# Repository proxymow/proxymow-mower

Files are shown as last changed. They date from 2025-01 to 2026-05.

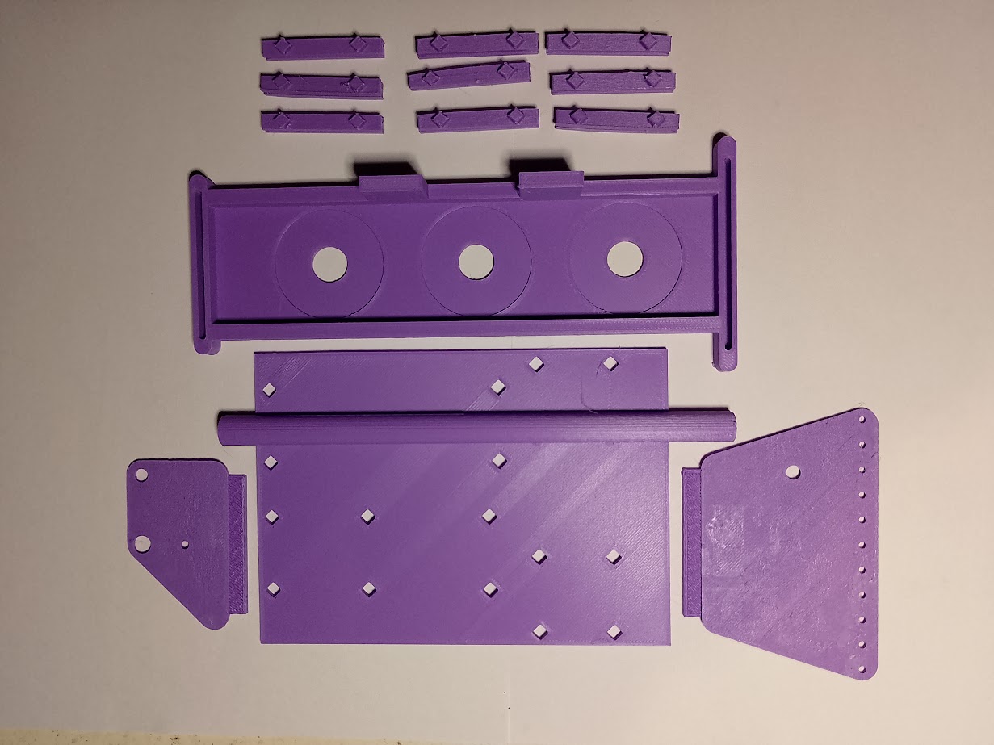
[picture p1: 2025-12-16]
3dprint-tracks/electronics-chassis/printed parts.jpg

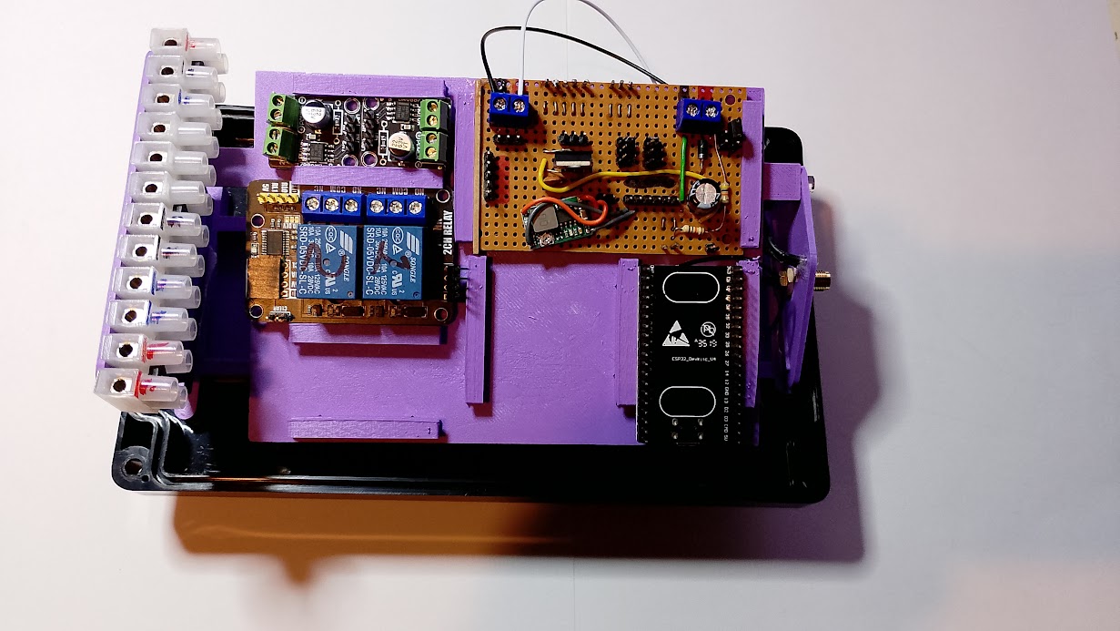
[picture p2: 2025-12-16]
3dprint-tracks/electronics-chassis/assembly.jpg

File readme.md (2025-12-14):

# Proxymow Automated Robot Lawn Mower (Mower)
## What the project does
Proxymow is a robotic lawn mower system that uses computer vision to locate and guide the mower. This repository contains the MicroPython source code for the mower device. The sister repository [Proxymow Server](https://github.com/proxymow/proxymow-server) contains the source code for the server.

## Why the project is useful
Proxymow differs from many robotic mowers:
* Does not rely on vulnerable boundary wires
* Does not use GPS or Bollards
* Does not need to be taught a route, supports plug-in mowing patterns
* Employs very low cost technology: Rasperry Pi, NodeMCU, RPI Pico, ESP32

## Getting started
Clone or Download the repo and change directory to the installation folder.

Edit utils.py to set up Wi-Fi access, and schematic.py to *wire up* your mower.

Use Thonny, or rshell to deploy the following MicroPython files to your device:
* main.py
* mower.py
* schematic.py
* utils.py
* shared_utils.py
* artic.py
* umotion_lib.py

Reset the device and use the test client to issue some commands:
```
    cd clients; python udp_client.py 
```

## Getting help
Read the documentation [module information](https://proxymow.co.uk/mower).

## Who maintains and contributes to the project
info@proxymow.co.uk

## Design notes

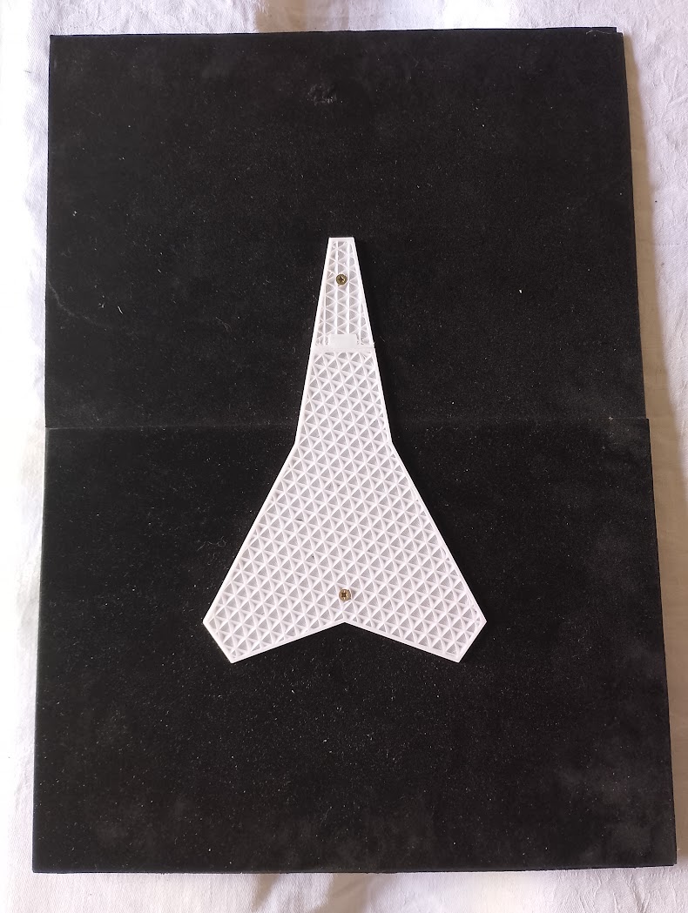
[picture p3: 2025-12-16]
3dprint-tracks/target/target mounted.jpg

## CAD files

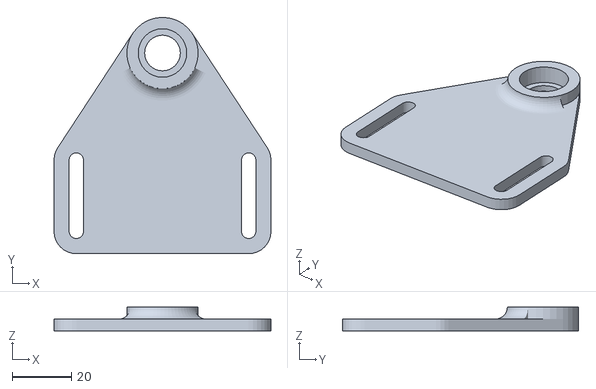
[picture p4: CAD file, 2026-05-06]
3dprint-tracks/bearing-plate/Bearing BackPlateMk2.stl
73.0 x 79.5 x 8.00

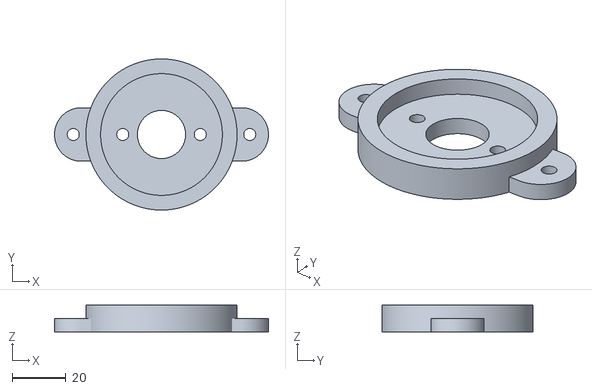
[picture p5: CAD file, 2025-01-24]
3dprint-tracks/cutter-motor-bracket/Cutter-Motor-Bracket.stl
80.0 x 56.5 x 10.0

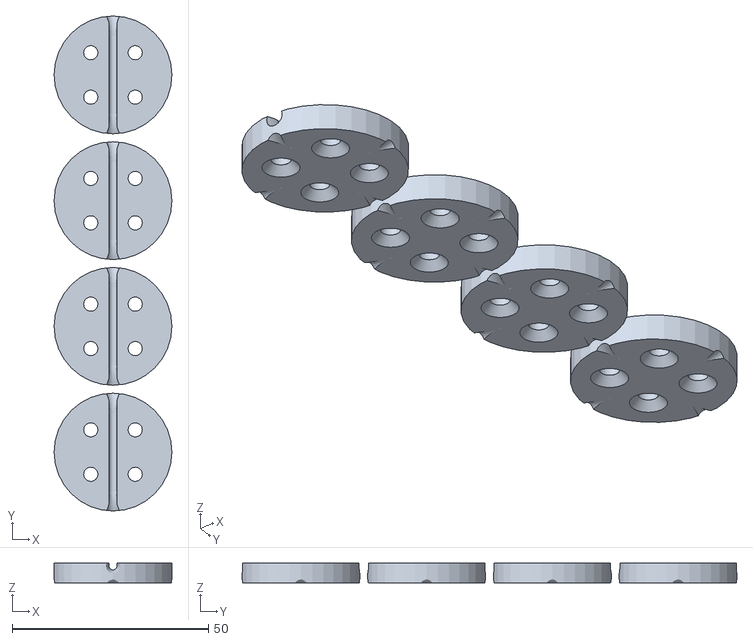
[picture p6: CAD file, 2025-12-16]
3dprint-tracks/cutter-wire-stack/Cutter-Wire-Stack.stl
30.0 x 126.0 x 5.00

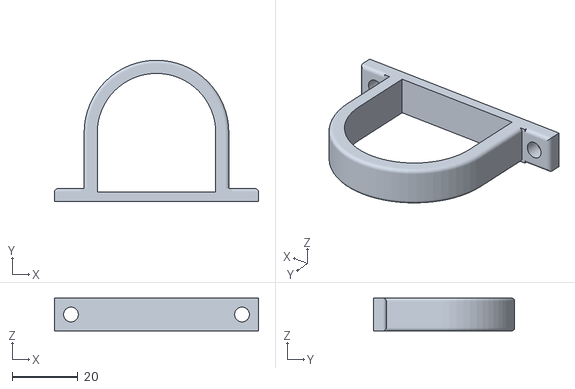
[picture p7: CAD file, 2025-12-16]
3dprint-tracks/drive-motor-bracket/Planetary Motor Bracket.stl
62.0 x 43.0 x 10.0

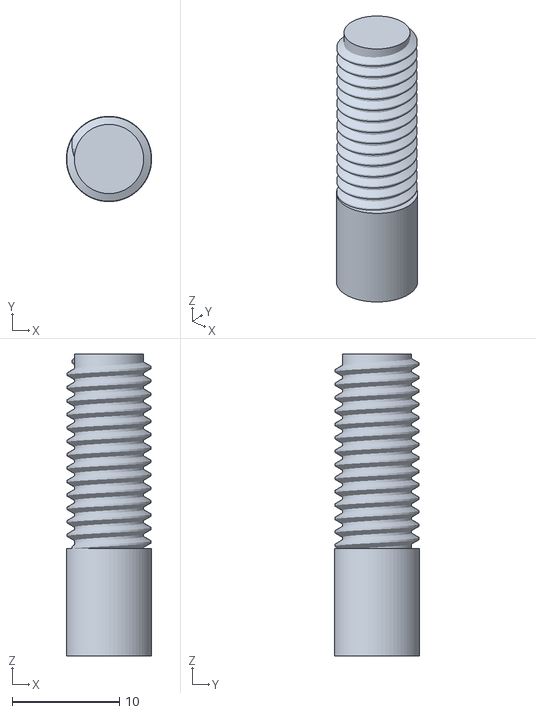
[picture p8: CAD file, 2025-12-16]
3dprint-tracks/drive-sprocket/Drive Sprocket Shaft.stl
7.95 x 7.95 x 28.1

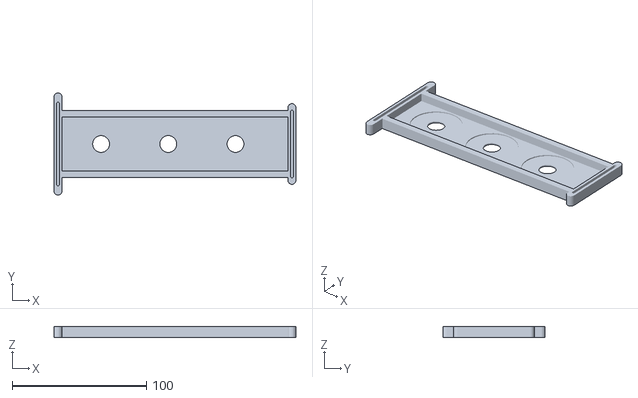
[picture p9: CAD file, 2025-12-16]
3dprint-tracks/electronics-chassis/chassis-base.stl
180.0 x 76.0 x 8.00

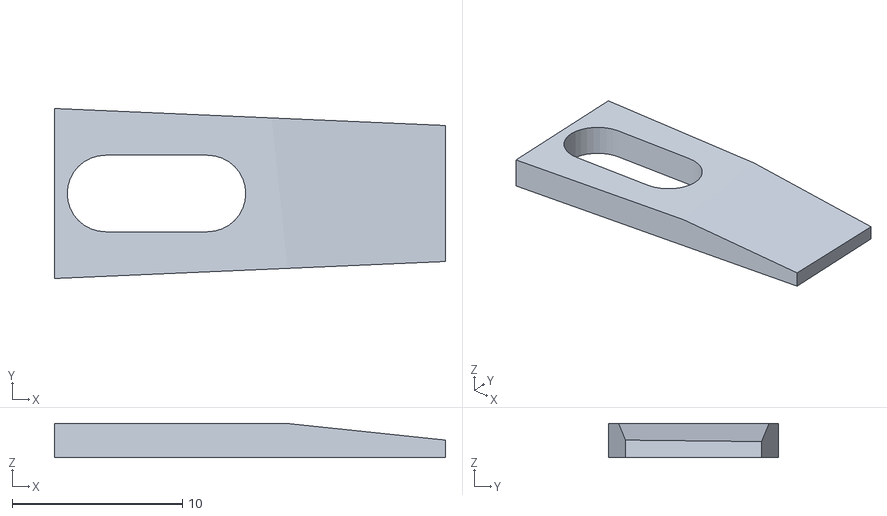
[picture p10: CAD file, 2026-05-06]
3dprint-tracks/idler-hub/scraper.stl
23.0 x 10.0 x 2.00

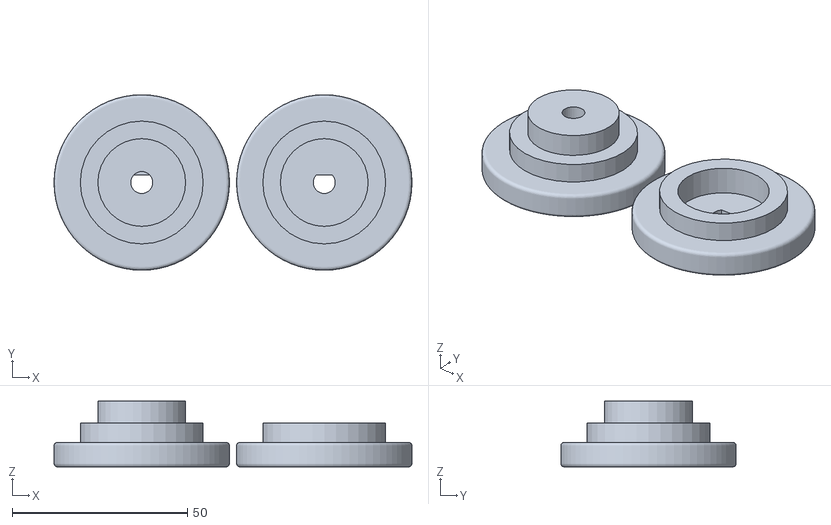
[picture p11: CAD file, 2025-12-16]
3dprint-tracks/idler-wheel/Idle Wheel.stl
102.0 x 50.0 x 18.8

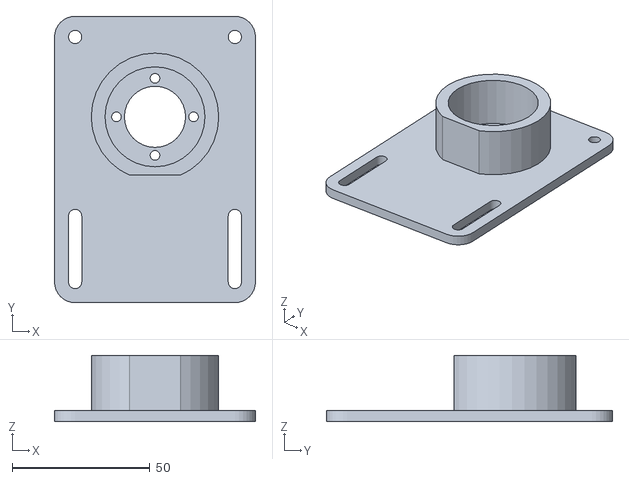
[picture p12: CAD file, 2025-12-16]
3dprint-tracks/motor-plate/Motor Plate.stl
73.0 x 104.0 x 24.0

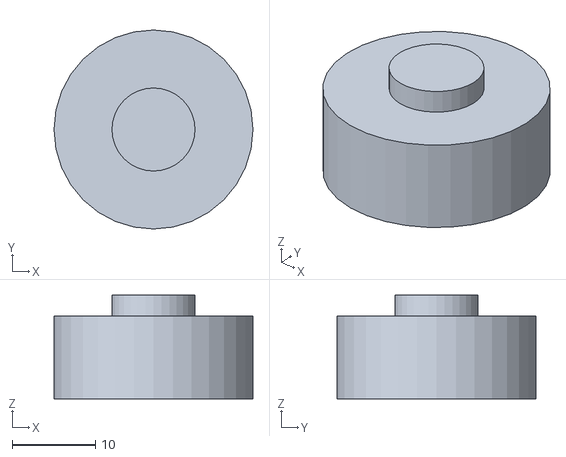
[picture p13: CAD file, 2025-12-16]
3dprint-tracks/roof-socket/Roof Plug.stl
23.9 x 23.9 x 12.5

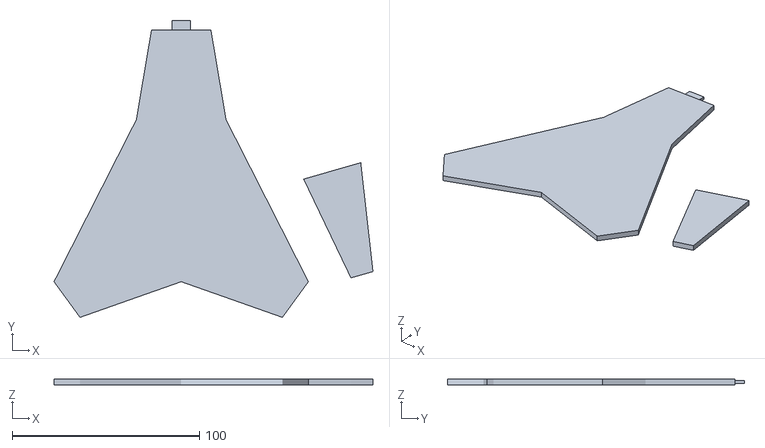
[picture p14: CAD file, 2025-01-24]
3dprint-tracks/target/Target-230.stl
170.2 x 158.3 x 3.00

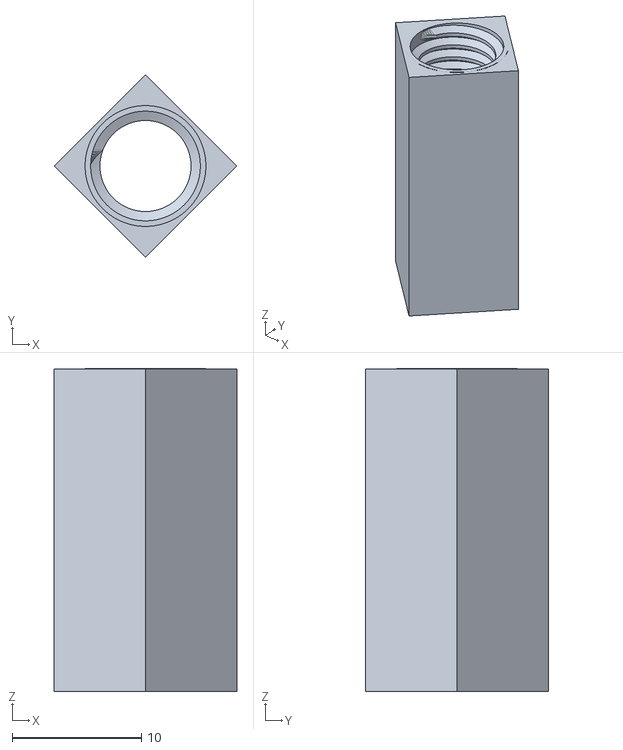
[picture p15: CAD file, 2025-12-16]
3dprint-tracks/tension-rod-adaptor/Hub Threaded Insert.stl
14.1 x 14.1 x 25.0

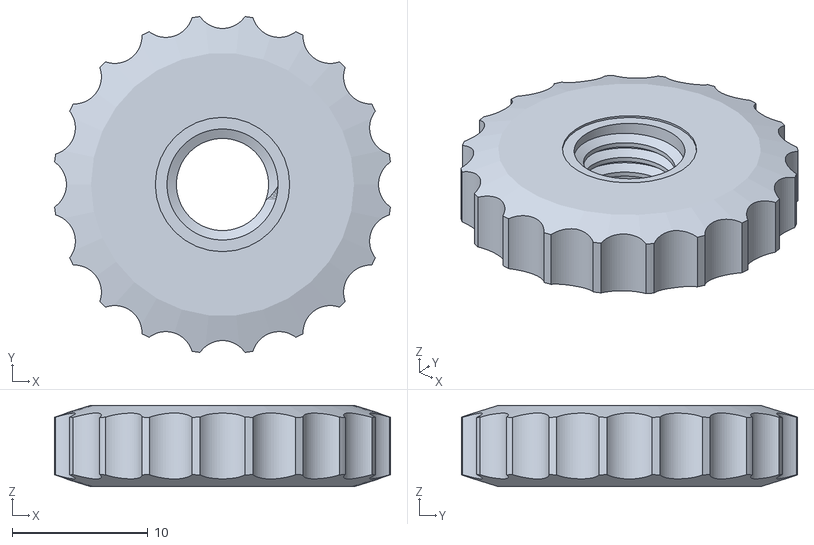
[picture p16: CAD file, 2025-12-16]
3dprint-tracks/thumbwheels/Thumbwheel.stl
24.8 x 24.8 x 6.00

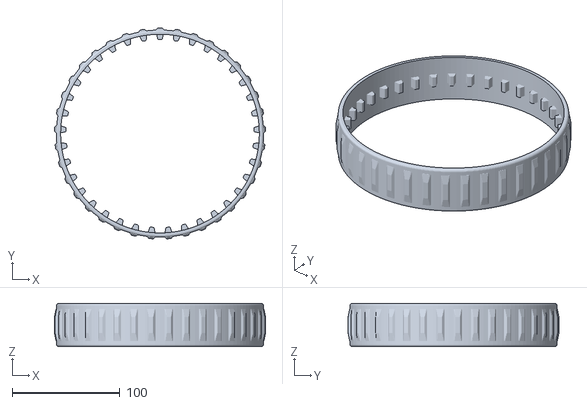
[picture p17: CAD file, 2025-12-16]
3dprint-tracks/track/Belt.stl
196.0 x 195.9 x 40.0

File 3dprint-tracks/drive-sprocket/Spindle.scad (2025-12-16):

//Spindle for Sprocket Components
include <../shared/Constants.scad>
use <threadlib/threadlib.scad>

module dee_shaft(hgt, dia, offset) {
    difference() {
        cylinder(h=hgt, d=dia, center=true, $fn=32);
        translate([0, dia - offset, 0]) cube([dia, dia, hgt+0.1], center=true);
        translate([0, -(dia - offset), 0]) cube([dia, dia, hgt+0.1], center=true);
    }
}

module spindle() {
     {
        rotate([0, 180, 0]) difference() {
            union() {
                cylinder(h=spindle_length, d=spindle_outer_dia, $fn=6, center=true);
                translate([0, 0, (spindle_length + spindle_shoulder_width)/2]) cylinder(h=spindle_shoulder_width, d=spindle_shoulder_dia, $fn=32, center=true);
            }
        translate([0, 0, (spindle_drive_shaft_length + 0.1)/2]) dee_shaft(spindle_drive_shaft_length, spindle_dee_shaft_dia, spindle_dee_shaft_offset);
        translate([0, 0, -(spindle_length/2)]) cylinder(h=spindle_length + 2, d=spindle_bearing_shaft_dia, center=true, $fn=32);
        }
        translate([0, 0, 0.5]) scale([spindle_thread_x_factor, spindle_thread_y_factor, spindle_thread_z_factor]) nut("M8", turns=spindle_thread_num_turns, Douter=9, $fn=6);
    }
}

spindle();

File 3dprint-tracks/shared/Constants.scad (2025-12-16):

/*
    Constants.scad contains all the global constants
*/
use <Tooth Profile.scad>

//idler hub
idle_bearing_od = 16;//mm
idle_bearing_fit_dia = idle_bearing_od * 1.03;//push-in fit for bearing
idle_bearing_thickness = 5.25;//push-in fit
hub_thickness = 15;
hub_dia = 24;
idle_shaft_hole_dia = 6.5;//clearance for 6mm shaft
scraper_fix_hole_dia = 4.5;//mm
idler_width = 25;//mm
idler_dia = 50;//mm
idler_spacing = 0.5;//mm
radial_spacing = 5;//mm
tube_insertion = 25;//mm
tube_outer_dim = 10;//10mm square tube
tube_dim = sqrt(tube_outer_dim^2 + tube_outer_dim^2) * 1.04;
echo("tube_outer_dim:", tube_outer_dim, "tube_dim:", tube_dim);

//idler wheel
idle_wheel_thickness = 25;
idle_wheel_dia = 50;
idle_shaft_dia = 6.25;//mm
tooth_space_thickness = 11;//mm
tooth_space_dia = 35;//mm
runner_thickness = (idle_wheel_thickness - tooth_space_thickness)/2;
edge_radius = 1;
dee_shaft_offset = 1;
spigot_scale_factor = 1.0;//grow spigot hole if necessary for a tight fit

//idler axle
idle_rod_dia = 5.92;//mm tight fit for bearing
idle_rod_length = 25 + (2 * 0.5) + (2 * 15) + (2 * 2);//mm idler width + 2 spacers + 2 hubs + 2 washers
echo("idle_rod_length", idle_rod_length);
idle_rod_cap_length = 2;//mm
idle_rod_clip_width = 1;//mm
idle_rod_clip_dia = 4.5;//mm

//knurled wheel and locknut
//knob parameters
KNOB_DIAM=25;
//screw parameters
SCREWHEAD_FACETOFACE=0;
SCREWHEAD_DEPTH=12;
THRU_HOLE_DIAM=9.5;
//grippy cutouts parameters
NUM_GRIP_CUTOUTS=20;
GRIP_CUTOUT_DIAM=4;
CUTOUT_RADIUS_ADJ=1;
KNURLED_WHEEL_HEIGHT=6;
KNURLED_WHEEL_NUM_TURNS = 3.5;
LOCKNUT_HEIGHT=3;
LOCKNUT_NUM_TURNS = 1.375;

//motor plate
gearbox_collar_hole_dia = 22.2;//mm
motor_plate_thickness = 4;//mm
motor_plate_corner_dia = 15;//mm
plan_motor_dia = 36.3;//mm
plan_shoulder_base_thickness = 3;// mm
plan_shoulder_thickness = 5;// mm
plan_shoulder_height = 20;// mm

//planetary motor bracket
pmb_motor_dia = 36;//mm 35.5 plus clearance
pmb_base_thickness = 3;//mm
pmb_foot_thickness = 5;//mm
pmb_width = 10;//mm
pmb_thickness = 4;//mm
pmb_chamfer_radius = 1;//mm
pmb_fix_hole_dia = 4.5;//mm

//bearing backplate
drive_bearing_bush_dia = 24;//mm
drive_bearing_od = 16;//mm
drive_bearing_fit_dia = drive_bearing_od * 1.02;//push fit for bearing
drive_bearing_recess = 6;//mm 

//drive sprocket
sprocket_spacing = 0.5;//mm
tooth_height = 5;//mm 4 + 1 to sink into cylinder

//tube clamp
clamp_width = 10;//mm
clamp_effect = 0.75;//mm
clamp_int_dia = 0.5;//mm
clamp_ext_dia = 2.5;//mm
clamp_fix_hole_dia = 4.8;//mm
clamp_washer_dia = 13;// for 12.5mm washer
clamp_washer_thickness = 1;//mm

//drive spindle
plan_motor_drive_shaft_dia = 8;//mm
spindle_outer_dia = 20;//mm fn=6 for hex
spindle_length = 25;//mm
spindle_shoulder_dia = 30;//mm
spindle_shoulder_width = 10;//mm
drive_sprocket_shaft_hole_dia = 8.32;//for 8mm shaft
spindle_dee_shaft_offset = 1;//mm
spindle_dee_shaft_dia = plan_motor_drive_shaft_dia * 1.0175;//mm interference fit
spindle_drive_shaft_length = 25;//mm shaft is 17.5 only 14mm of which is D'eed
spindle_bearing_shaft_dia = 9.3;//space for M8 thread
spindle_thread_num_turns = 9;
spindle_thread_x_factor = 1.04;
spindle_thread_y_factor = 1.04;
spindle_thread_z_factor = 1.0;

//drive sprocket shaft
drive_sprocket_shaft_num_turns = 14;
bearing_section_length = 10;//mm
back_bearing_stub_dia = 7.95;//mm for 8mm hole in bearing

//drive sprocket cog
tth_num_teeth = 9;
tth_pitch_angle = 360 / tth_num_teeth;
drive_sprocket_dia = 50;
tooth_depression = 1.1;//to smooth base fillets
sprock_tooth_x_scale = 0.8;//put space between teeth
sprock_tooth_y_scale = 1.05;//
sprock_thickness = 11;//mm for a 7|11|7 sandwich
tth_sprock_press_angle = 5;
tth_tooth_pitch = 8;
tth_root_fillet_radius = 1;
tth_tooth_height = 5;
sprock_tooth_profile_pts = tooth_points(tth_sprock_press_angle, tth_tooth_pitch, tth_root_fillet_radius, tth_tooth_height);

//drive plain cog
plain_cog_dia = 50;
plain_cog_thickness = 7;
plain_cog_rim_thickness = 3;//mm

//just for assembly
wheelbase = 200;//mm horizontal distance between idle wheel centres
track_triangle_height = 60;//mm vertical distance between drive motor and tube centres

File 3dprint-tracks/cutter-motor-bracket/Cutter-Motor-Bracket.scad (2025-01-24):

/*
    Proxymow Mower - Cutter Motor Bracket
    For 775 Type 12V DC Motor
    Print in TPU to provide anti-vibration properties
*/
$fa=1;
$fs=0.4;
body_height = 10;//mm
body_dia = 56.5;//mm
cutout_height = 5;//mm
motor_body_dia = 45.5;//mm
motor_collar_dia = 18;//mm
motor_fixing_centres = 29;//mm
motor_fix_hole_dia = 4.5;//mm
fix_hole_dia = 4.5;//mm
foot_dia = 20;//mm
foot_height= 5;//mm
foot_extent = 30;//mm
fixing_centres = 66;//mm

module bracket_body() {
    //outer ring
    difference() {
        cylinder(h=body_height, d=body_dia);
        translate([0, 0, body_height/2]) cylinder(h=body_height, d=motor_body_dia);
    }
    //feet
    hull() {
        translate([foot_extent,0,0]) cylinder(h=foot_height, d=foot_dia);
        translate([-foot_extent,0,0]) cylinder(h=foot_height, d=foot_dia);
    }
}
module cm_bracket() {
    difference() {
        bracket_body();
        //central hole
        translate([0,0,-1]) cylinder(h=body_height, d=motor_collar_dia);
        //motor fixings
        translate([motor_fixing_centres/2,0,-1]) cylinder(h=body_height, d=motor_fix_hole_dia);
        translate([-motor_fixing_centres/2,0,-1]) cylinder(h=body_height, d=motor_fix_hole_dia);
        //mounting holes
        translate([fixing_centres/2,0,-1]) cylinder(h=body_height, d=fix_hole_dia);
        translate([-fixing_centres/2,0,-1]) cylinder(h=body_height, d=fix_hole_dia);
    }
}
cm_bracket();

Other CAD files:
3dprint-tracks/tube-clamp/Tube Clamp.stl
3dprint/battery-mount/Battery-Foot.stl
3dprint/component-tray/rp2-pico.stl
3dprint/drive-motor-bracket/Drive-Motor-Bracket.stl
3dprint-tracks/drive-motor-bracket/Planetary Motor Bracket.scad
3dprint-tracks/assembly/Assembly.scad
3dprint-tracks/bearing-plate/Bearing BackPlate.scad
3dprint-tracks/bearing-plate/Bearing BackPlate.stl
3dprint-tracks/bearing-plate/Bearing BackPlateMk2.scad
3dprint-tracks/cutter-wire-stack/Cutter-Wire-Stack.scad
3dprint-tracks/drive-sprocket/Drive Plain Cog.scad
3dprint-tracks/drive-sprocket/Drive Plain Cog.stl
3dprint-tracks/drive-sprocket/Drive Sprocket Cog.scad
3dprint-tracks/drive-sprocket/Drive Sprocket Cog.stl
3dprint-tracks/drive-sprocket/Drive Sprocket Shaft.scad
3dprint-tracks/drive-sprocket/Spindle.stl
3dprint-tracks/electronics-chassis/Chassis.scad
3dprint-tracks/electronics-chassis/chassis-platform.stl
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

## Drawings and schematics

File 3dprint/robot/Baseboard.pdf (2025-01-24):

## Cutout to aid alignment of

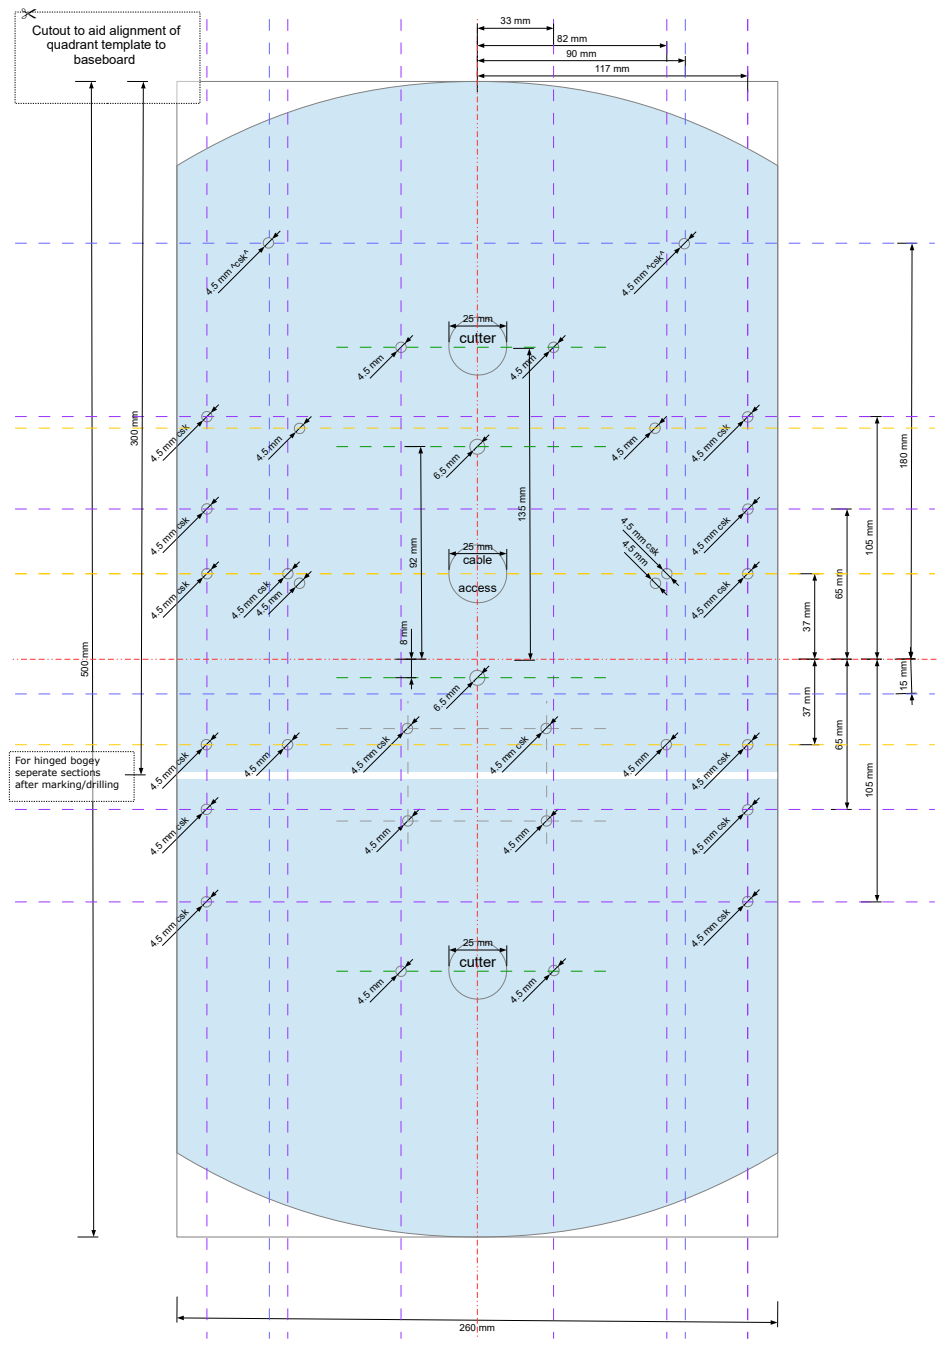
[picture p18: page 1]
4.5 mm csk; cutter; cable; access; ^csk^

quadrant template to
baseboard

For hinged bogey
seperate sections
after marking/drilling

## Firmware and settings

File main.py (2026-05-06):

import sys
import machine as m
import micropython
import schematic

# enable emergency exception buffer for exceptions in isrs
micropython.alloc_emergency_exception_buf(100)

try:
    # load mower
    print('launching mower')
    import mower
except Exception as err:
    msg = 'error launching mower: ' + str(err)
    print(msg)
    # Open the file in 'append' mode to keep previous error logs
    with open("error_log.txt", "a") as f:
        f.write("\n--- main Error ---\n")
        sys.print_exception(err, f)
    m.reset()

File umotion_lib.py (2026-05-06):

from math import degrees, radians
from time import ticks_ms, sleep
import machine
from machine import Timer
import json
from sys import platform # esp32 | rp2
import schematic as scm
import utils
import artic

x_m = y_m = theta_rad = 0
min_adc = 1024

# control functions
def stop():
    # Emergency Stop
    cutter(0, -1)
    abort()
    utils.log('Emergency Stop Activated!')
def abort():
    # Abort Movement
    for pwm in scm.pwms: # deactivate all
        artic.set_duty(pwm, 0)
def sweep(left_speed, right_speed, duration):
    return artic.sweep(left_speed, right_speed, duration)
def readadcs():
    analogs = []
    if scm.adc_enabled:
        for i in range(len(scm.adcs)):
            # read_u16 read a raw analog value in the range 0-65535
            analogs.append(scm.adcs[i].read_u16() // 64)
    else:
        analogs = []
    return analogs
def get_telemetry():
    # update telemetry values
    global min_adc
    cut1_val = cut2_val = -1
    if scm.i2c_enabled:
        try:
            byte_state = scm.i2c.readfrom_mem(scm.i2c_reg, scm.RELAY_STATE_REG, 1)
            state = int.from_bytes(byte_state, 'big')
            utils.log('read relay state: {}'.format(state))
            cut1_val = state & 1
            cut2_val = (state & 2) // 2
        except Exception as e:
            utils.log('Error reading i2c in get telemetry: ' + str(e))
    anlgs = readadcs()
    if platform != 'rp2':
        if len(anlgs) > 0 and anlgs[0] > 512:
            min_adc = min(anlgs[0], min_adc)
            anlgs[1] = min_adc
    utils.telem['analogs'] = anlgs
    utils.telem['cutter1'] = cut1_val
    utils.telem['cutter2'] = cut2_val
    utils.telem['last-update'] = ticks_ms()
    utils.telem['reset-cause'] = str(machine.reset_cause())
    result = json.dumps(utils.telem, separators=(',', ':'))
    return result
def get_pose():
    # assemble pose json in degrees
    return '[{},{},{}]'.format(x_m, y_m, degrees(theta_rad))
def set_pose(xm_in, ym_in, thetadeg_in, axle_track_m=None, tyre_velocity_mps=None):
    global x_m, y_m, theta_rad
    utils.log('setting pose incoming: {:.0f}@({:.2f}, {:.2f}) {} {}'.format(
        xm_in, ym_in, thetadeg_in, axle_track_m, tyre_velocity_mps)
    )
    # update pose
    if axle_track_m is not None:
        scm.axle_track_m = axle_track_m
    if tyre_velocity_mps is not None:
        scm.tyre_velocity_mps = tyre_velocity_mps
    x_m, y_m, theta_rad = xm_in, ym_in, radians(thetadeg_in)
    utils.log('setting pose: {:.0f}@({:.2f}, {:.2f})'.format(degrees(theta_rad), x_m, y_m))
    return 0
def set_priority_essid(essid=None):
    # set the preferred access point in utils
    if any([essid.startswith(ps) for ps in utils.PREFERRED_ESSIDS]):
        utils.PRIORITY_ESSID = essid
        utils.log('set_priority_essid: ' + essid)
        utils.checks()
        return 0
    else:
        utils.log('set_priority_essid error unrecognised essid: ' + essid)
        return -1
def cutter(addr_in, mode):
    '''
        addr may be a binary address (mode -1)
        or a channel index (modes 0 & 1) 
    '''
    result = -1
    if scm.i2c_enabled:
        utils.log('Cutter addr:{} mode:{} intmode:{} type:{}'.format(addr_in, mode, int(mode), type(mode)))
        cutter_state_bytes = scm.i2c.readfrom_mem(scm.i2c_reg, scm.RELAY_STATE_REG, 2)
        cur_state = int.from_bytes(cutter_state_bytes, 'big') // 256
        addr = int(addr_in)
        mask = 2**addr
        if mode > 0.5:
            # independent channel set mode
            utils.log('Cutter {} ON'.format(addr + 1))
            addr = cur_state | mask
        elif mode >= 0.0:
            # independent channel clear mode
            utils.log('Cutter {} OFF'.format(addr + 1))
            addr = cur_state & ~mask
        addr_byte_array = (addr, 0) # (address, timer)
        addr_bytes = bytes(addr_byte_array)
        try:
            utils.log('Cutter address bytes {} Writing...'.format(addr_bytes))    
            scm.i2c.writeto_mem(scm.i2c_reg, scm.RELAY_STATE_REG, addr_bytes)
            result = 3
        except Exception:
            utils.log('Cutter address {} Write Failed'.format(addr))
            result = 0
        # pause to allow settling
        sleep(2.5)
    return result
def cancel(_t=None):
    # switch off led - active low
    scm.out_pins['act_led'].value(True)    
def led(duration=200):
    # switch on led
    scm.out_pins['act_led'].value(False)  
    scm.led_on_timer.init(period=int(duration), mode=Timer.ONE_SHOT,callback=lambda t:cancel(t))
def reset():
    stop()
    utils.log('Rebooting in 5 seconds...')
    scm.led_off_timer.init(period=5000, mode=Timer.ONE_SHOT,callback=lambda t:machine.reset())
    return 1

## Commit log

2025-01-24 Openscad Design Files and 3D Print Files
    [Assembly.scad, Axle.scad, Axle.stl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]
2025-01-25 Modify hinge elevation, add assembly stl
    [robot-assembly.scad]
2025-02-17 nid replaced with uid as pico has same first 6 chars
    [schematic.py]
2025-04-14 Create Hinge.stl
    stl file added
    [Hinge.stl]
2025-08-12 Update artic.py
    Accommodate ESP32, PWM Inversion and limit duty to 100%
2025-08-12 Update mower.py
    Make space for REPL, cutter disable on reset
    [mower.py]
2025-08-12 Update schematic.py
    PWM Inversion, 10&16 bit duty, esp32 example
2025-12-14 PWM, ADC and ESP32 GPIO Changes
    Changed PWM frequency to 2khz
    Renamed led to act_led
    Added Velocity Ramp-Up and Ramp-Down Constants
    Re-assigned GPIO Pins used by ESP32
    PWM ensure duty is initialised to zero (uPython bug)
    Corrected ESP32 Analog range
    Added Init Complete led flash
    [schematic.py]
2025-12-14 Revised to implement Cosenoidal Velocity Ramping
2025-12-14 Fixed set_pose bug, improved reset
    [umotion_lib.py]
2025-12-14 Moved led function from umotion_lib
2025-12-16 Openscad and stl files for the Tracked Robot Mower
    New robot mower design, with rubber tracks printed in TPU. Offers better performance than wheeled model in most scenarios.
    [Assembly.scad, Bearing BackPlate.scad, Bearing BackPlate.stl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]
2026-01-01 Problem with Velocity Ramping when reversing resolved
    [artic.py]
2026-05-06 improved velocity ramping
2026-05-06 improved backplate allowing axle to protrude through bearing
    [Bearing BackPlateMk2.scad, Bearing BackPlateMk2.stl]
2026-05-06 scraper to bolt to hub - keeps idler from getting clogged
    [Scraper.scad, scraper.stl]
